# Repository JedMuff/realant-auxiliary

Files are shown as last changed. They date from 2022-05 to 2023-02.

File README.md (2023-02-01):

RealAnt Auxiliary
=================
robot_transparent
The RealAnt Auxiliary contains additioning documentation, improved designs and some simple walk gait code for the RealAnt designed by Ote Robotics at Aalto University (https://github.com/OteRobotics/realant).

The repository provides improvements relating to robustness and usability. These are related to the screw fittings and the repairability of the design. Design improvements included:
1. soft attachments to dampen damage to the robot (see 'stl_softparts' folder)
2. proper board mounting for easy construction (see 'stl_standard' folder)
3. access hatches for ease of use and repairability (see 'stl_standard' folder)
4. a stand for a motion tracking marker(used inreinforcement learning) (see 'stl_standard' folder)

Additionally with an improved robot design, some code was developed that utilized DYNAMIXEL AX-12A actuators to produce walking gaits and gestures the quadruped robot could use for initial functionality testing (see 'code' folder). 

Watch the youtube video here: https://www.youtube.com/watch?v=h07QOblhzB0.

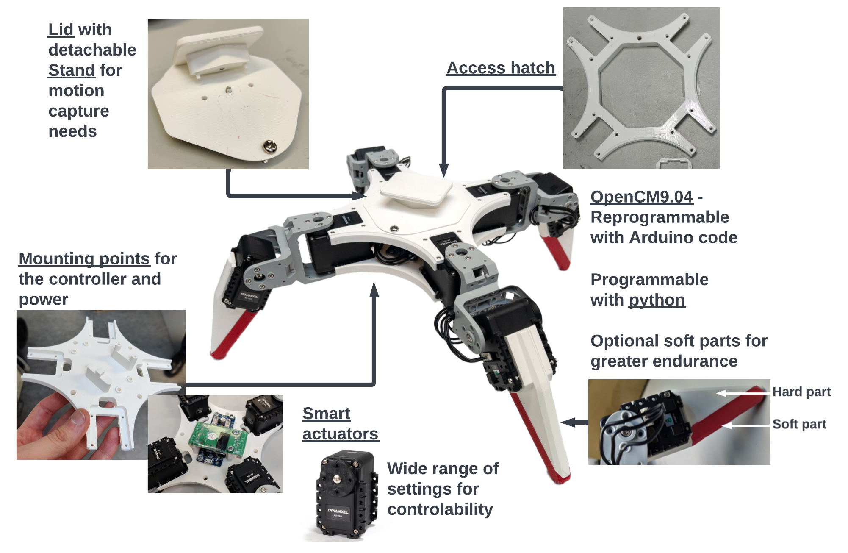
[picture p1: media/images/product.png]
product


More detailed documentation on contruction and usage where made, this can be found in the **docs** folder. 

# Structure of the GitHub
The key folders in this repository are described below, see the README kept in each directory for more details:

- **code:** Contains all the code needed for running the robot, including some simple gaits for testing.
- **docs:** Contains all the documentation for constructing and using the robot.
- **media:** Some images used in the documentation with some additional bonus images of the robot. Also contains a video made about the project. 
- **stl_softparts:** Contains the soft parts made.
- **stl_standard:** Contains the improved parts made. A modified spacer was added that improves the fit to the leg.

# Get in Contact
If you want to contribute to this repo or need any help these are the people to contact.
* Jed Muff - GitHub Managment and general help (https://www.linkedin.com/in/jed-muff/) 
* Eric Hannus - Working with the code (https://www.linkedin.com/in/eric-hannus/)
* Antti Sippola - Standard 3D printed parts (https://www.linkedin.com/in/anttisippola/)
* Julius Mikala - Soft 3D printed parts (https://www.linkedin.com/in/julius-mikala-594791178/)
# Links
**RealAnt (developed by Ote Robtics) GitHub:** https://github.com/OteRobotics/realant

**Reinforcement Learning with RealAnt** – https://github.com/AaltoVision/realant-rl

**RealAnt Auxiliary GitHub:** https://github.com/JedMuff/realant-auxiliary

**Intelligent Robotics Research Group Webpage:** https://irobotics.aalto.fi/ 

**Wiki page:** https://wiki.aalto.fi/display/AEEproject/Building+a+quadruped+robot+for+reinforcement+learning+research

**Research group page about this project:** https://irobotics.aalto.fi/building-a-quadruped-robot/

# Resources
**AX12A - EManual:** https://emanual.robotis.com/docs/en/dxl/ax/ax-12a/

**AX12 - Usermanual:** https://www.crustcrawler.com/products/bioloid/docs/AX-12.pdf

**OpenCM 9.04 - EManual:** https://emanual.robotis.com/docs/en/parts/controller/opencm904/

**Credits**:
Jed Muff, Jere Vepsä, Eric Hannus, Antti Sippola, Julius Mikala, Rituraj Kaushik, Ote Robotics

# Copyright and License

The files in this repository share files with the original [RealAnt](https://github.com/OteRobotics/realant) repository. As such the repository shares Copyright (c) 2020 with Ote Robotics Ltd and Aalto University and is licensed under MIT license. To the best of our ability we have labelled which files belong under the Ote Robotics Ltd license and which files come under the authors of this repository Copyright (c) 2023 Jed Muff, Eric Hannus, Antti Sippola, Julius Mikala, Jere Vespä.

See LICENSE for details.

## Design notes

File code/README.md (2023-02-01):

## Code Notes
The following scripts are used to test and control the robot:
-	antproxy.py
-	ant_server.py
-	tester.py
-	commander.py
-	move_set.py

The **antproxy.py** and **ant_sever.py** scripts are used to set up communication with the robot using ZeroMQ. 
These scripts are unchanged from the versions used in the original RealAnt, except for row 20 in **ant_server.py**.
which should be modified to reflect the port used for the USB connection to the robot.

The **tester.py** script is used to test individual servos, selected by their Dynamixel ID. 
The code contains functions for writing a position to a servo, testing the full motion range of a servo, and resetting 
the servos to their default positions. The script prints messages to the terminal to guide the user.

The **commander.py** requires the “keyboard” Python library. It contains functions for pre-programmed linear and rotational motion. 
The script also calls other pre-programmed actions stored in the **move_set.py** file. The W, A, S and D keys are used for linear motion,  
Q is used for counter-clockwise rotation and E for clockwise rotation, and keys 1-9 are used to run pre-programmed actions 
stored in the **move_set.py** file.

How to use:
1)	Connect power supply and USB to the robot
2)	Change line 20 in **ant_server.py** to reflect the USB port used. Default is /dev/ttyACM0.
3)	Run from the command line the following scripts: **antproxy.py**, **ant_server.py**, and **tester.py** or **commander.py**

The **ant11_cmd_dxl.ino** is the Arduino code for the OpenCM9.04 control board, and it is unchanged from the version found in the original RealAnt.

The .ino files in the folders "general_test_codes" and "servo_config_code" are not needed to run the robot, but they can be used to configure and test Dynamixel AX-12A servos via the OpenCM9.04 control board. More details are found under **/docs/dynamixel_A12A_guide.md** heading **'Accessing the Control Table via the OpenCM9.04 controller'**.

# Copyright and License

Copyright is split in this directory. Each file specifies who the copyright belongs to.

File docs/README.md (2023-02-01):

# Documentation Notes
This folder contains the following files:

- **U2d2_adapter_guide.md:** A guide on how to use the U2D2 adapter with Dynamixel Wizard 2.0 and DynamixelSDK. Used for configuring the actuators.
- **construction.md:** A step by step guide with images on how to make the robot. Also contains parts list.
- **construction.png:** An abstracted diagram showing the construction process.
- **dynamixel_A12A_guide.md:** A guide describing how the Dynamixel AX-12A servos work and how to configure them with the OpenCM board (not nessasary if using the U2d2_adapter).
- **parts_catalog.pdf:** A table showing the 3D printed parts and the setting used.
- **wiring_diagram.png:** Overall wiring diagram of the robot. The order of wiring on the boards does not matter. The ID numbers for the actuators does matter depending on the code that is used. The diagram shows what was used, with the front right actuators being 1 at the top and 2 at the bottom. This ID orientation was used to allow for easy visualization of the actuators when testing.

## Description of the Robot
The robot consists of a cover and base plates, to protect and structure the robot and legs for the robot to walk on. Both plates and leg parts are made with a 3D printer. The robot utilizes eight Dynamixel AX-12A servos for movements, two in each leg, and has eight degrees of freedom. 

Movements are sent by the Arduino based OpenCM9.04 control board and powered by a SMPS2Dynamixel power supply connector. The robot is controlled by a computer with a serial connection via USB cable using python scripts. A visual orientation tracker can be added on top of the robot's cover plate.

# Copyright and License

All documentation in realant-auxiliary/docs/ is Copyright (c) 2023 Jed Muff, Eric Hannus, Antti Sippola, Julius Mikala, Jere Vespä under MIT license. 

See LICENSE for details.See LICENSE for details.

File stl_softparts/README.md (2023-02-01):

# Some Details About Soft Parts
*For details on suggested settings to use please refer to the parts catalog (**realant-auxiliary/docs/parts_catalogue.pdf**).These settings produced suitably soft parts, as with a higher infill density was too rigid for dampening.* 

*3D printers used were either the Ultimaker S3 or S5.*

*For details about how to attach the soft parts please refer to steps 1.1 and 6.1 of the construction documentation (**realant-auxiliary/docs/construction.md**).*

The regular legs of the Real-Ant robot are reasonably fit for their intended use. However one issue identified stems from the robot's primary use: reinforcement learning. This use case makes the Real-Ant likely to make more erratic motions and even slam itself to the ground. These motions might cause some durability problems for the robot such as screws coming loose.

One solution is using thread locking fluid. The thread locking fluid only solves the issue by fastening the screws, but it does not remove the shocks caused by the robot moving. Another solution was to change the design of the robot to incorporate soft parts.

## Designs
It was observed that the soft parts needed to be situated at the bottom of the leg and the bottom plate. The soft parts at the bottom plate are required because the
robot can strike the ground with its body first. 

Several designs for both the leg and the body plates were tested before these designs where settled upon. 

The leg piece simply substitutes soft filiment where necessary.
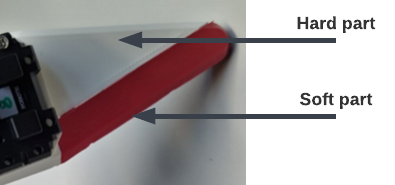
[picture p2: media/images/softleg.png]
softleg


The body plate protenction is in the form of simple soft tubes attached to the actuator connector with metal wire.
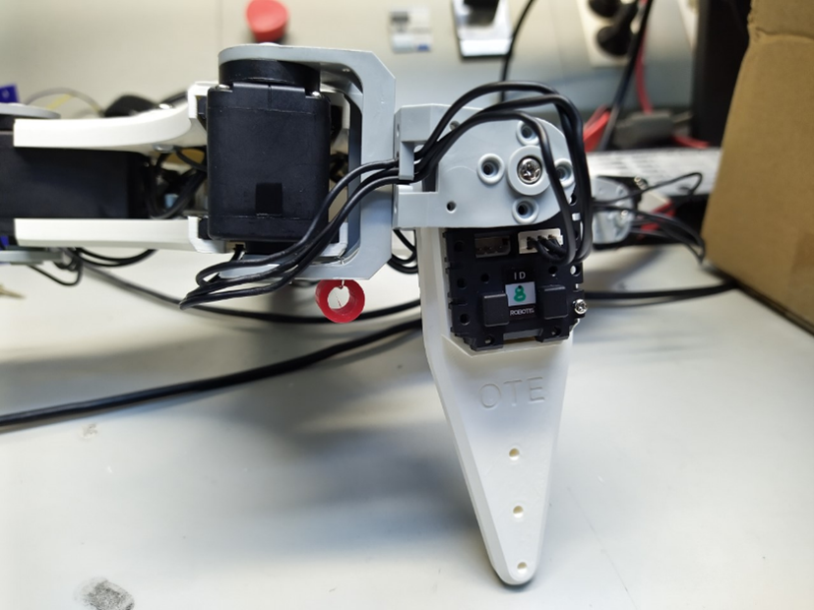
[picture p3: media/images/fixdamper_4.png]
fixdamper_4


# Copyright and License

leg.stl - Copyright (c) 2020 with Ote Robotics Ltd and Aalto University. Under MIT license. Copyright (c) 2023 Jed Muff, Eric Hannus, Antti Sippola, Julius Mikala, Jere Vespä. Under MIT license.

leg_damper.stl, round_joint_damper.stl - Copyright (c) 2023 Jed Muff, Eric Hannus, Antti Sippola, Julius Mikala, Jere Vespä. Under MIT license.

See LICENSE for details.

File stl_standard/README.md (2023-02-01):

# Details About Standard Parts

*For details about construction please refer to the construction documentation (**realant-auxiliary/docs/construction.md**).*

The body assembly of the robot serves two purposes. Firstly, it provides a structural element connecting the four leg assemblies. Secondly, it houses the electronics that power and control the actuators.

The general idea of the original body structure was kept with the new design. With the new design,the plates have similar attachments for the actuators, similar curves on the outer edges, and the actuator cables run through similar holes. However, unlike the original plates, the new design uses different parts for the top and bottom plates. This was required due to the addition of an access hatch and component mounting structures. The new design also adds parts for covering the hatch and attaching optional motion tracking markers.

# Copyright and License

bottom_plate.stl, modified_spacer.stl - Copyright (c) 2020 with Ote Robotics Ltd and Aalto University. Under MIT license.

optitrack_stand.stl, top_cover.stl, top_plate.stl - Copyright (c) 2023 Jed Muff, Eric Hannus, Antti Sippola, Julius Mikala, Jere Vespä. Under MIT license.

See LICENSE for details.

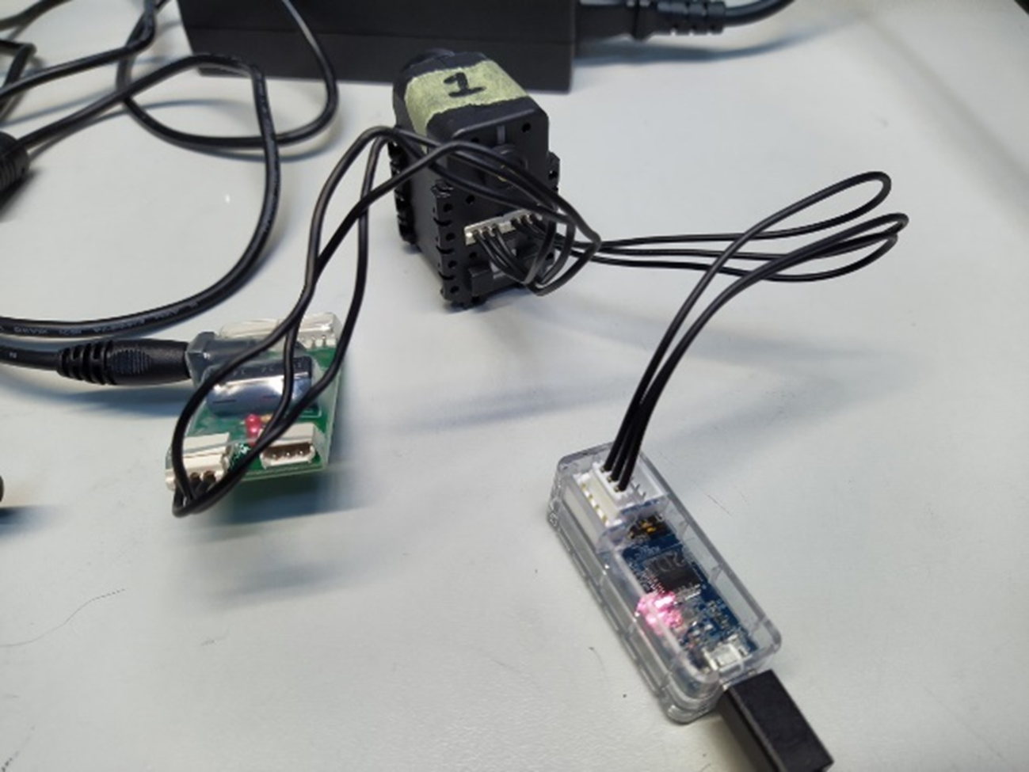
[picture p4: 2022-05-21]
media/images/U2D2_connection_2.png

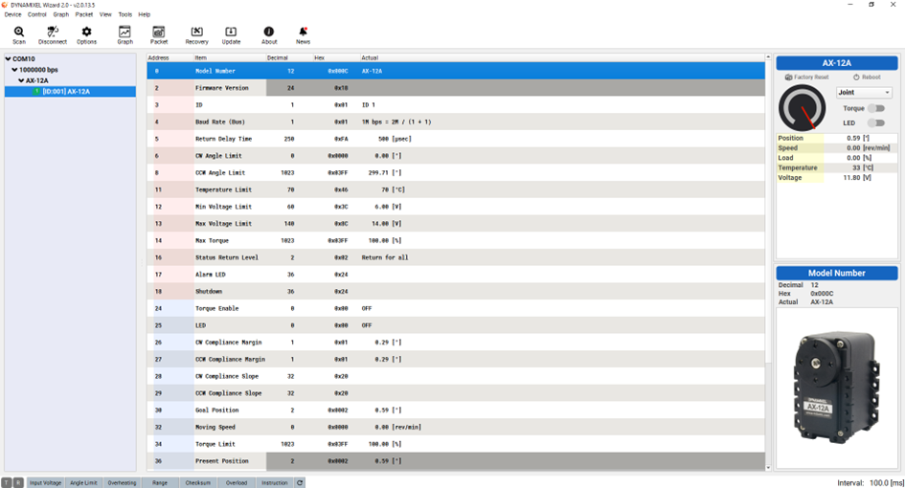
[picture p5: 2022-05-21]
media/images/Wizard_interface_1.png

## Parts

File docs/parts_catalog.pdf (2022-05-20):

## 3D Printed Parts Catalog

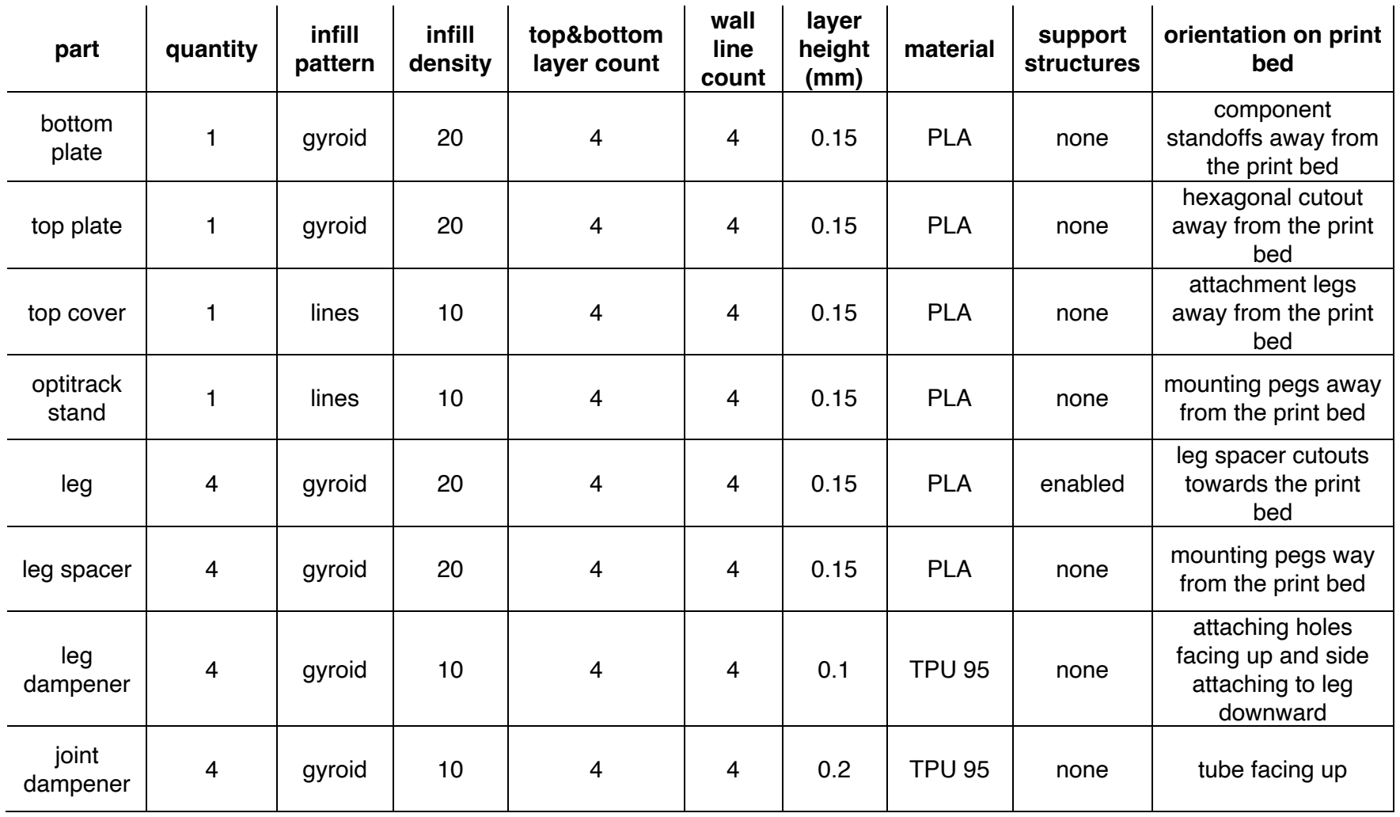
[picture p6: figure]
part; quantity; infill; pattern; infill density; top&bottom layer count; wall line count; layer height (mm); material; support; structures; orientation on print bed; bottom; plate; gyroid; PLA; none; component standoffs away from the print bed; top plate; hexagonal cutout away from the print bed; top cover; lines; attachment legs away from the print bed; optitrack; stand; mounting pegs away; from the print bed; leg; enabled; leg spacer cutouts towards the print bed; leg spacer; mounting pegs way; dampener; TPU 95; attaching holes facing up and side attaching to leg downward; joint; tube facing up

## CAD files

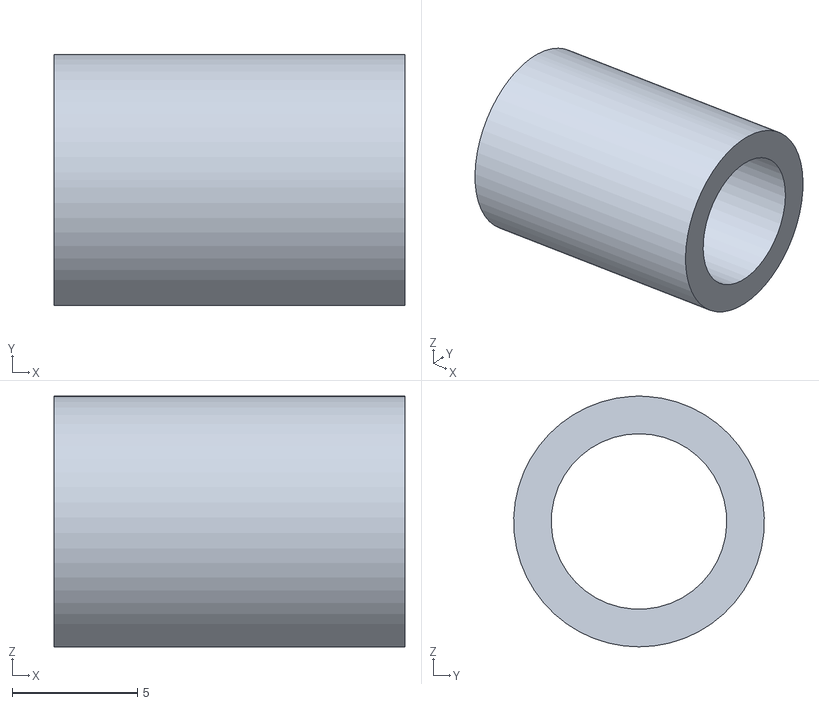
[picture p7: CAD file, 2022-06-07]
stl_softparts/round_joint_damper.stl
14.0 x 10.00 x 10.0

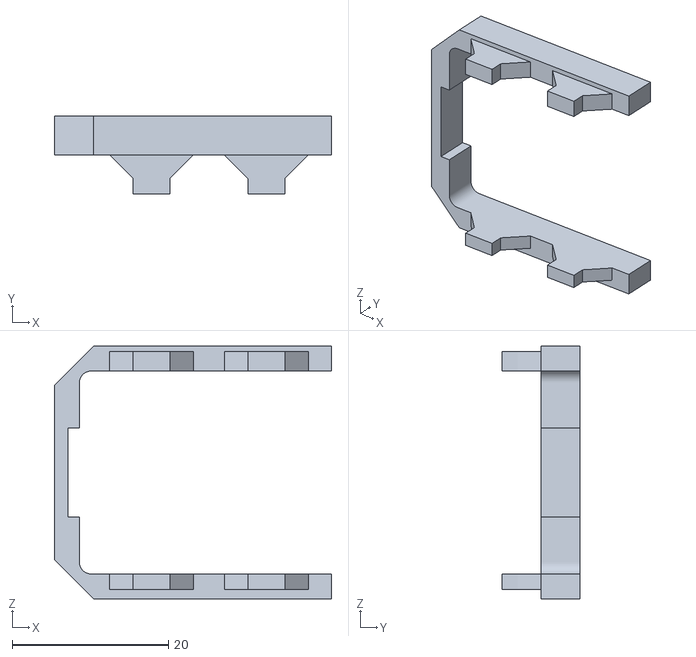
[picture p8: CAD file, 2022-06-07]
stl_standard/modified_spacer.stl
35.5 x 10.0 x 32.4

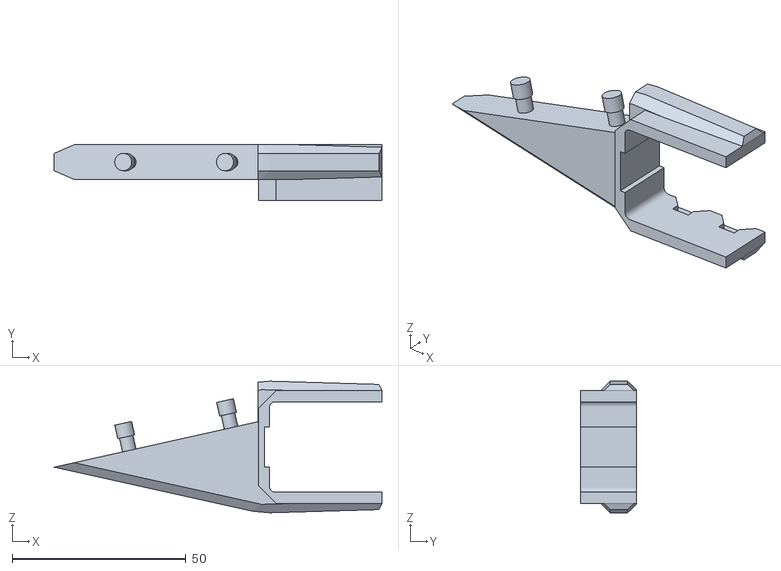
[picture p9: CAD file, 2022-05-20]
stl_softparts/leg.stl
94.3 x 16.0 x 37.9

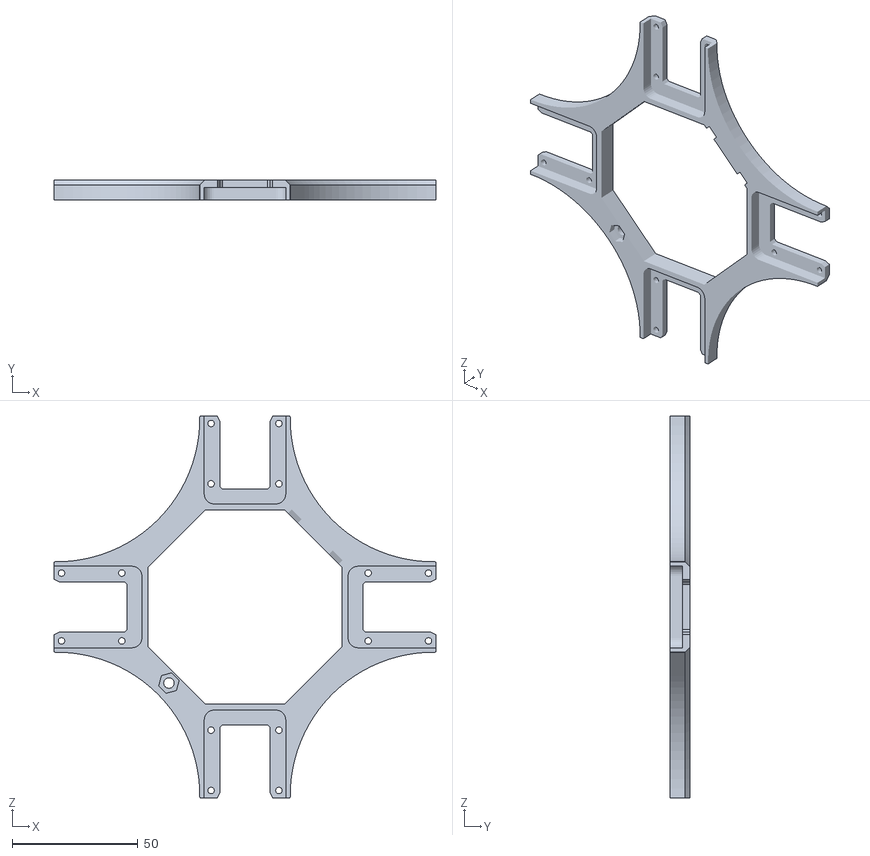
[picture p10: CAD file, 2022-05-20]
stl_standard/top_plate.stl
152.0 x 8.00 x 152.0

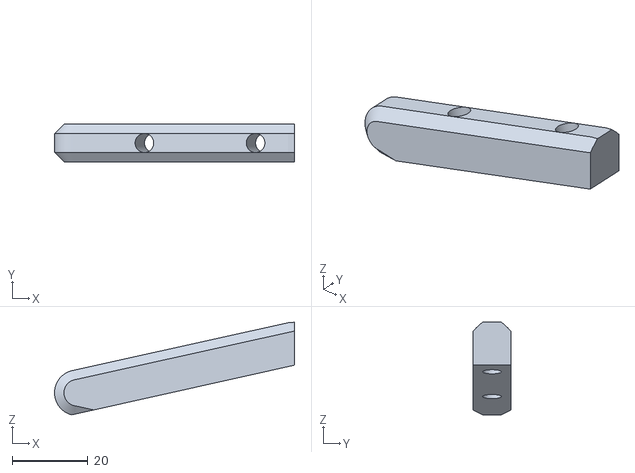
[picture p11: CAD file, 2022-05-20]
stl_softparts/leg_damper.stl
63.2 x 10.0 x 24.4

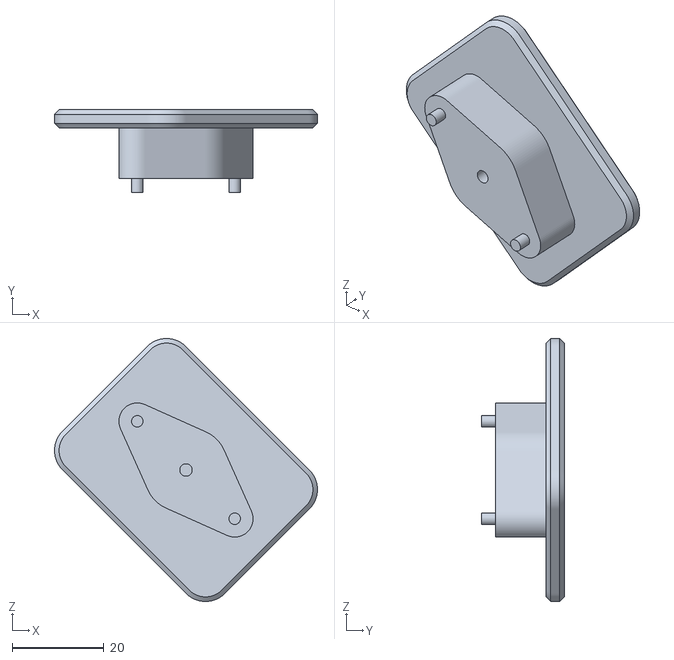
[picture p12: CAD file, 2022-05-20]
stl_standard/optitrack_stand.stl
57.3 x 18.0 x 57.3

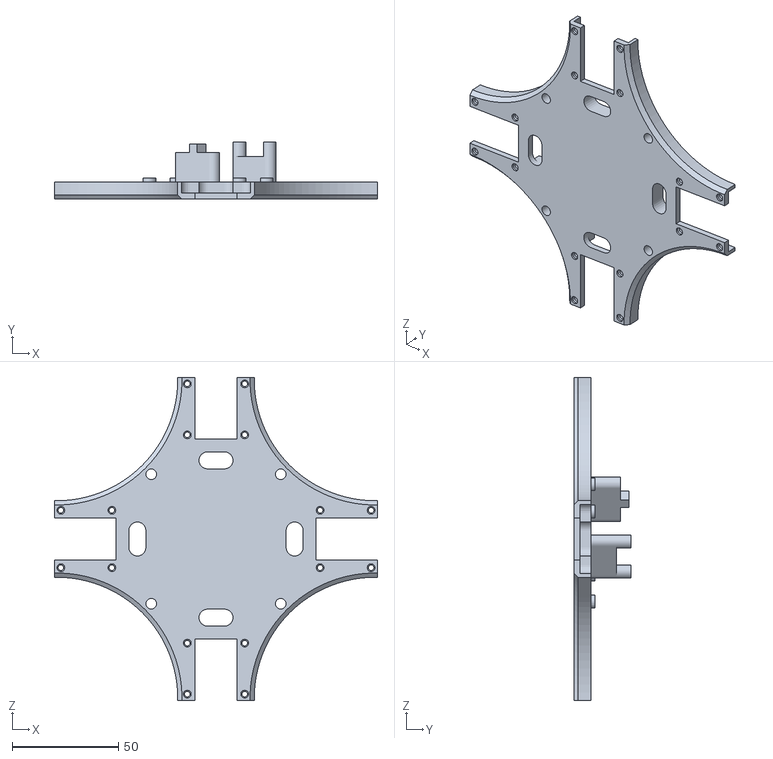
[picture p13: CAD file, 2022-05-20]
stl_standard/bottom_plate.stl
152.0 x 27.0 x 152.0

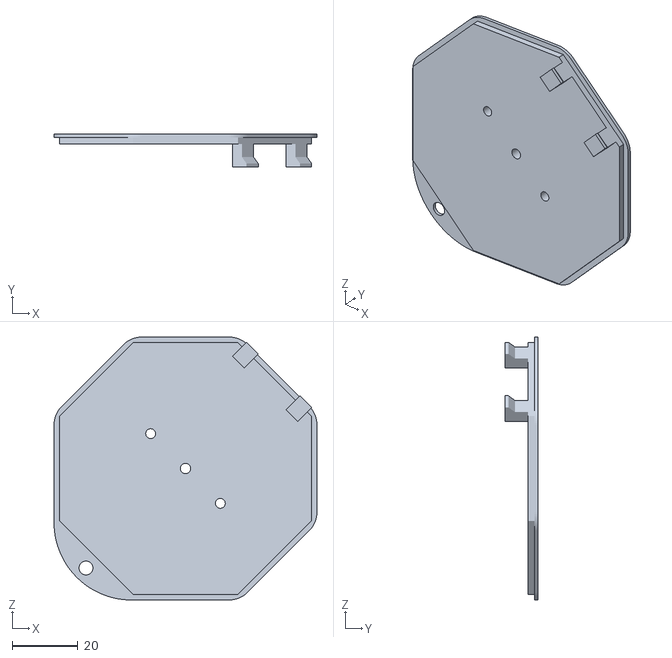
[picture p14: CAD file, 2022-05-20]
stl_standard/top_cover.stl
80.0 x 10.0 x 80.0

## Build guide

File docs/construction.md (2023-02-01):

# Preliminary Configuration of the Electronic Parts
## OpenCM9.04 Board

1.	U2D2 adapter or Arduino Uno
2.	OpenCM9.04 Board
3.	Dynamixel AX12 Actuators
4.	If U2D2 adapter, also need the appropriate wires
5.	If Arduino Uno, need Arduino USB connector and 3 Male to Female jumper wires

**Step 1 Configuring the Actuators -** The actuators need to be set up so that they have IDs ranging from 1 to 8 and no set limits. This can be done by either using the U2D2 adapter or an Arduino Uno. For each method please refer to the following documents:

* **U2D2 adapter**: “How to use the U2D2 adapter with Dynamixel Wizard 2.0 and DynamixelSDK”
* **Arduino Uno**: “Guide to Dynamixel AX-12A servos”

**Step 2 Configuring OpenCM board** - Install Arduino and setup Robotis OpenCM9.04 board support (refer to [OpenCM 9.04 e-manual](https://emanual.robotis.com/docs/en/parts/controller/opencm904/) 8.3. Arduino IDE) , and then upload the OpenCM9.04 firmware from ant11_cmd_dxl folder in this GitHub.

# Construction
## Parts Needed
1.	OpenCM9.04 Board
2.	Dynamixel AX12 Actuators (x8)
3.	Dynamixel AX12 Screws (that come with Dynamixel AX12s)
4.	Dynamixel AX12 support frames (that come with Dynamixel AX12s)
5.	Dynamixel AX/MX series (TTL) wire (x9)
6.	3D printed leg (x4) – Standard or soft version
7.	3D printed leg spacer (x4)
8.	3D printed Bottom body Plate
9.	3D printed Top Body plate
10.	SMPS2Dynamixel Board
11.	10mm M4 screws (x4)
12.	10mm M3 screws (x2)

## Optional Parts
1.	Steel wire
2.	Joint damper (x4)
3.	3D printed lid
4.	10 mm M4 screw
5.	M4 Nut
6.	3D printed stand
7.	10 mm M3 screw
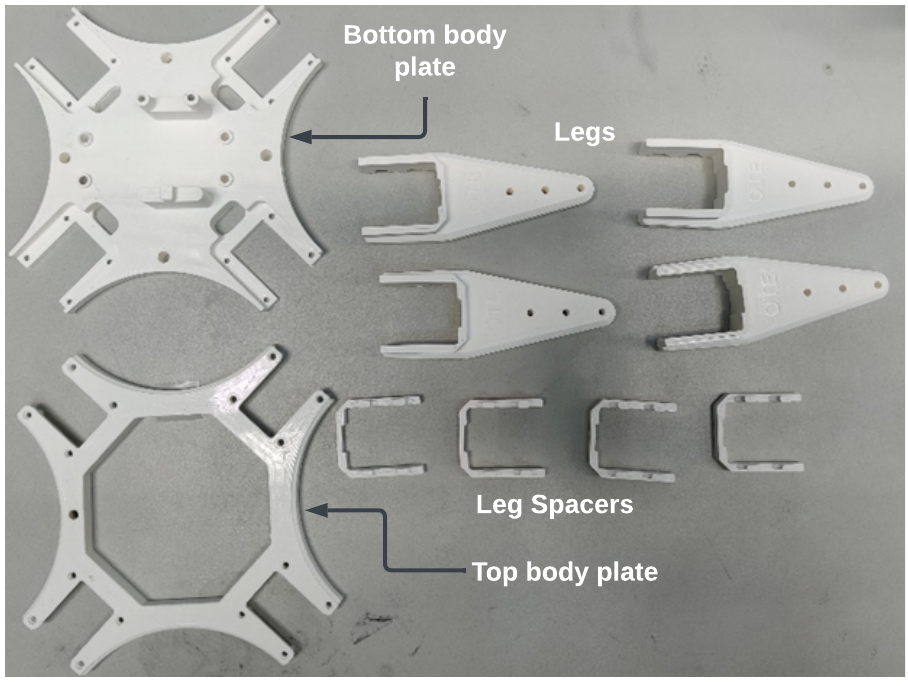
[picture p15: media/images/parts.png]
Parts


**Step 1 Priming the Legs** - The leg spacers need to be attached to the legs. To do this you may need to sand down the grooves in the leg and use a mallet to push the spacer into place. Don't apply too much force however as it may break the print. A smooth connection between the two needs to be ensured so that there is enough space to slide onto the actuator. This is done for all 4 legs.
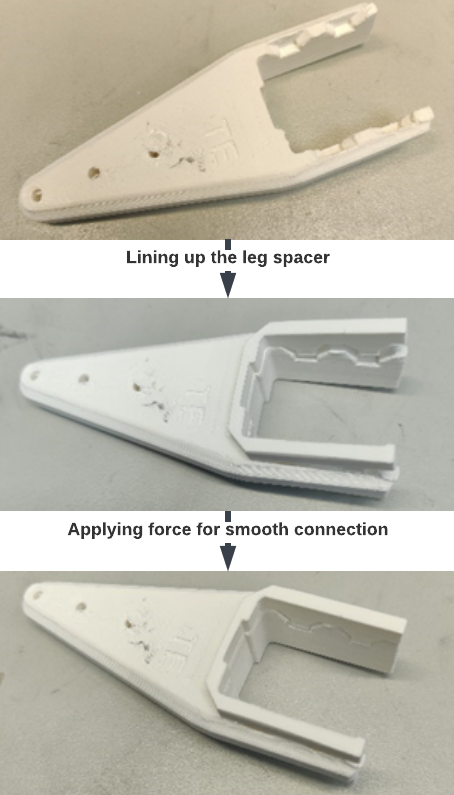
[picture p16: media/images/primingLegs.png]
primingLegs


**Step 1.1 (Optional) Fixing the soft Legs** - If you have opted for the soft legs, this is where the attachments are fitted on. This is simply done by sliding it onto the leg.

softleg

**Step 2 Priming the OpenCM Board** - Solder on the TTL headers (x4 all facing the same direction) onto the OpenCM Board.

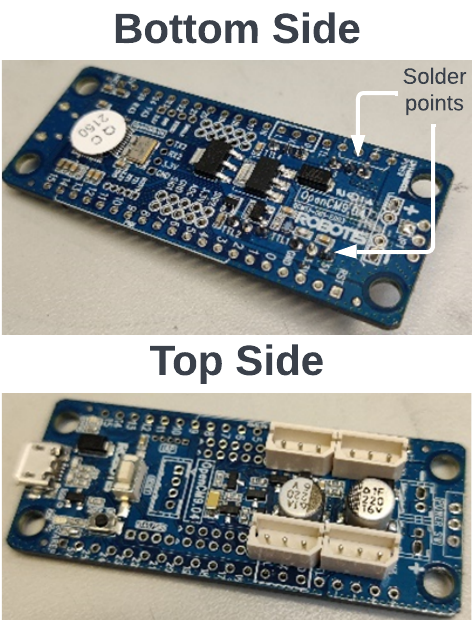
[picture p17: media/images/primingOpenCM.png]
primingOpenCM


**Step 3 Priming the SMPS2Dynamixel Board** - The SMPS2Dynamixel Board is prepared by cutting small holes in the film where 2 screw holes are. It is the two screw holes closest to the power connector. These holes are needed for mounting the board.
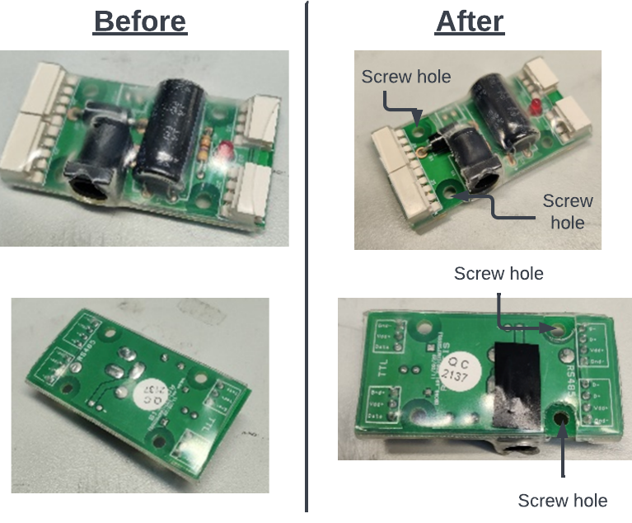
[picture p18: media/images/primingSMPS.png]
primingSMPS


**Step 4 Attaching the Legs to the Actuators** - The legs are attached to the actuators through friction. The legs should slide onto the actuators with a bit of force. If the grip seems too loose, then screws can be used to add more friction. This is done for all 4 legs.
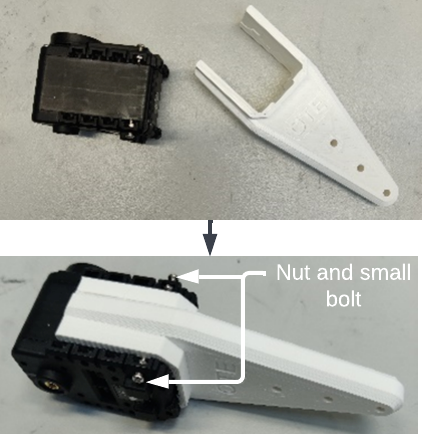
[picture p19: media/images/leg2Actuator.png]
leg2Actuator


**Step 5 Connecting the Support Frames** - Support frames are provided with the AX12's, along with screws. These first need to be connected with screws and bolts, 4 for each 2 supports for 1 leg. 16 screws and bolts are used overall for each leg.

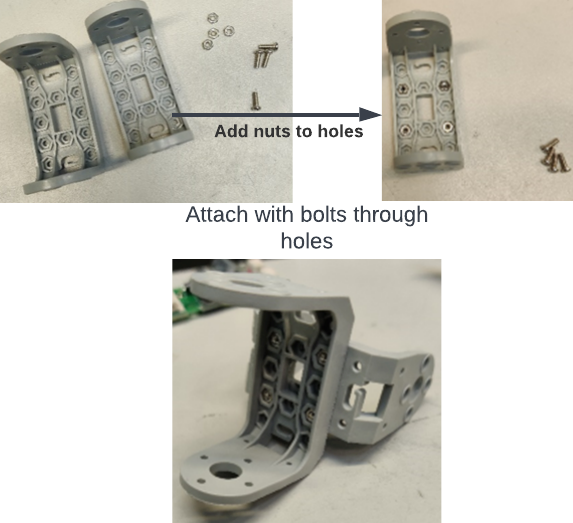
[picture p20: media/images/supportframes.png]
supportframes


**Step 6 Final Construction of the Leg** - Next the support frames are connected to the actuators, this is done once again with screws. Each connection requires 1 bigger screw and washer on one side and 4 smaller screws on the other. This is done for all 4 legs.

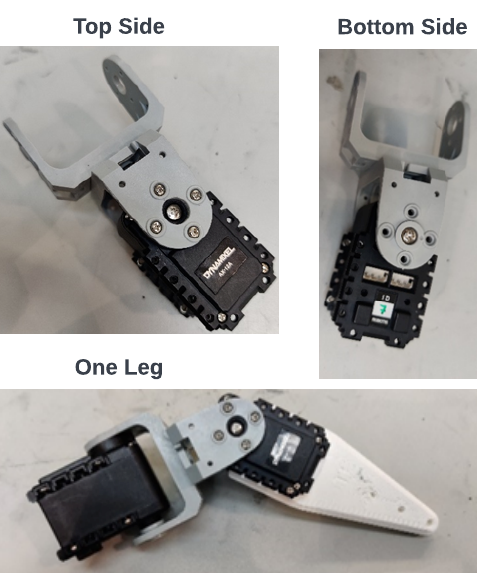
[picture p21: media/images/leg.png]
leg


**Step 6.1 (Optional) Fixing the Dampers** - 
1. Fit the joint damper to a piece of steel wire and push the wire through the holes in the plastic frame:
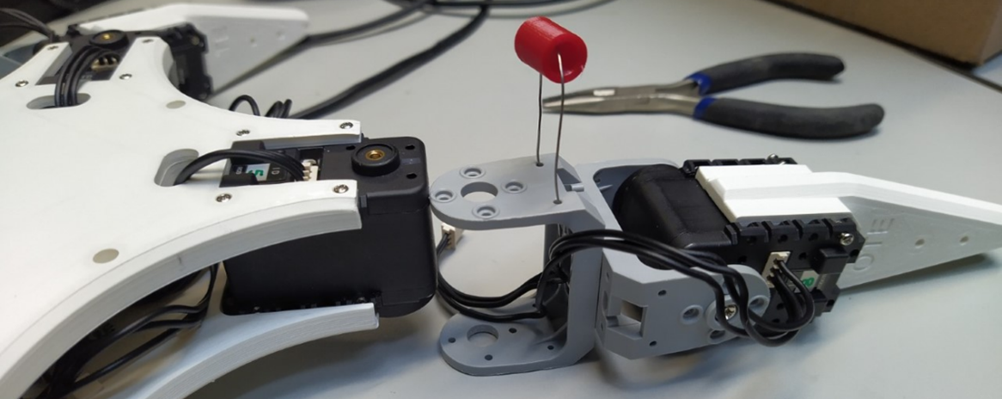
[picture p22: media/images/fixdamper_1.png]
fixdamper_1

1. Push the wire through and tighten it from the inside of the frame by twisting the steel wire:
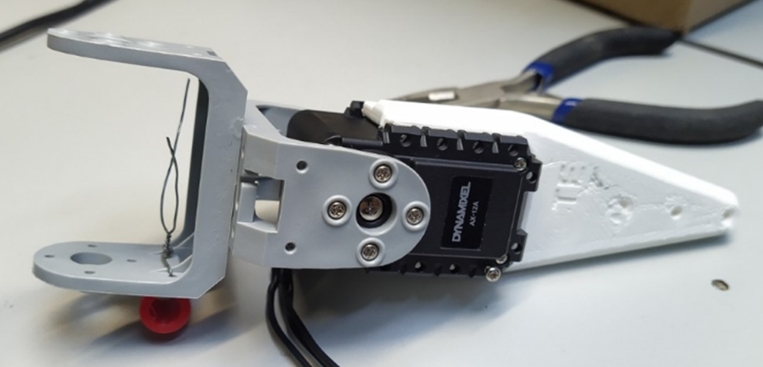
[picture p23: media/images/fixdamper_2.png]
fixdamper_2

3. Cut off any excess length of steel wire so it does not interfere with the joint movement, and finally re-attach the leg:
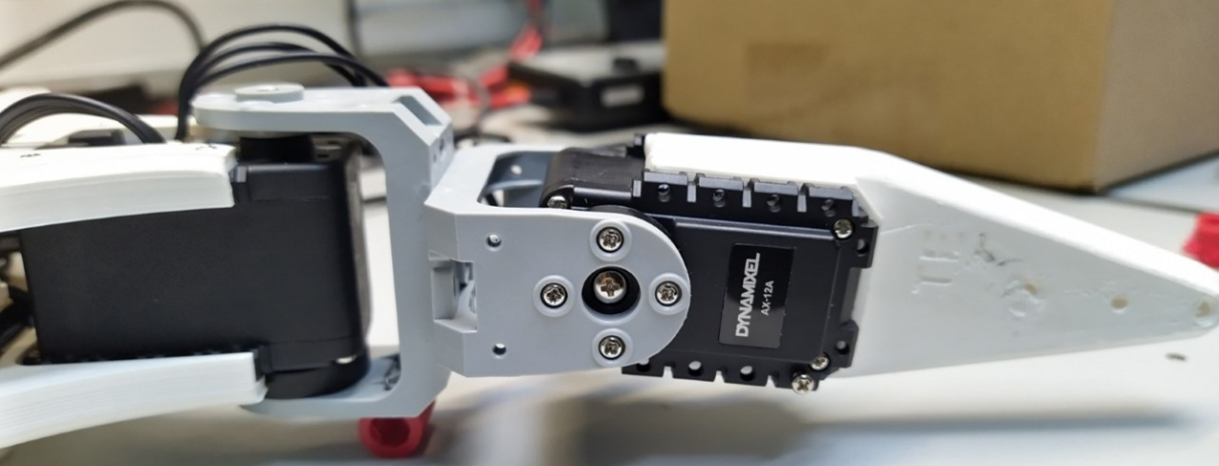
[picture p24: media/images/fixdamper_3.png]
fixdamper_3

4. Note that the wire cannot be routed through the slot in the frame piece closer to the body, as the joint damper is in the way. Route the wires through the slot in the other frame piece and try to keep the wire as tight as possible (while still allowing full motion of the joint!) near the body of the servo so that the wires do not drag under the robot:
fixdamper_4
**Step 7 Fit the Bottom Plate** - The bottom plate is fitted by simply by screwing it in the top actuators with screws provided by the AX12's.
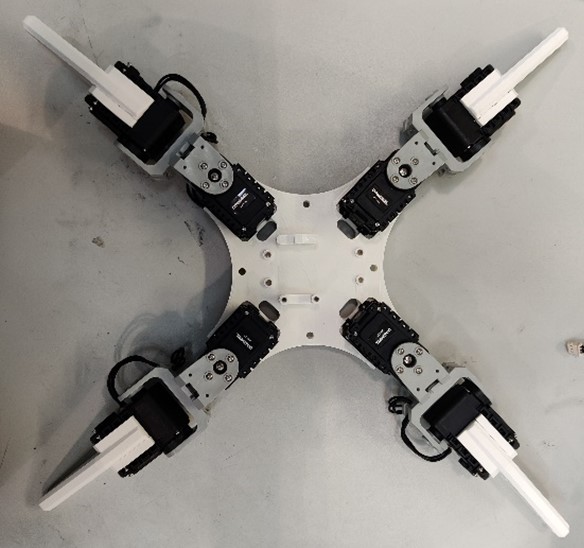
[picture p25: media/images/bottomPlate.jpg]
bottomPlate

**Step 8 Fit the OpenCM Board** - The OpenCM board is fitted with 4 10mm M4 screws. To screw the board in a bit of force is required to drill into the 3D printed holes.
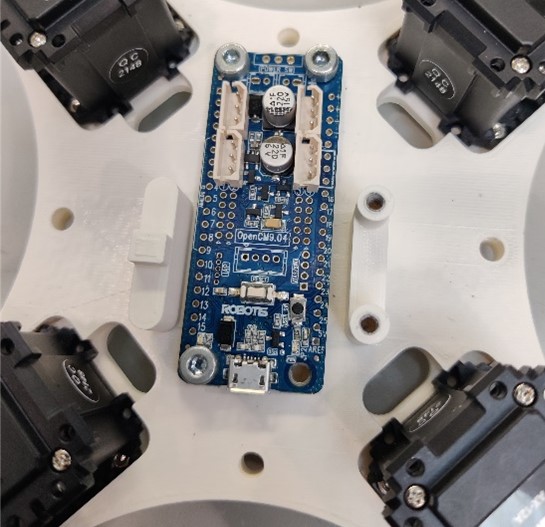
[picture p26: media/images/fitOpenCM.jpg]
fitOpenCM

**Step 9 Fit the SMPS2Dynamixel Board** - Next the SMPS2Dynamixel Board is fitted on top. Ensure it is facing the right direction and has the right orientation. Screw it in with 2 10mm M3 screws, it may require a bit of force to drill the screws into the drill holes.
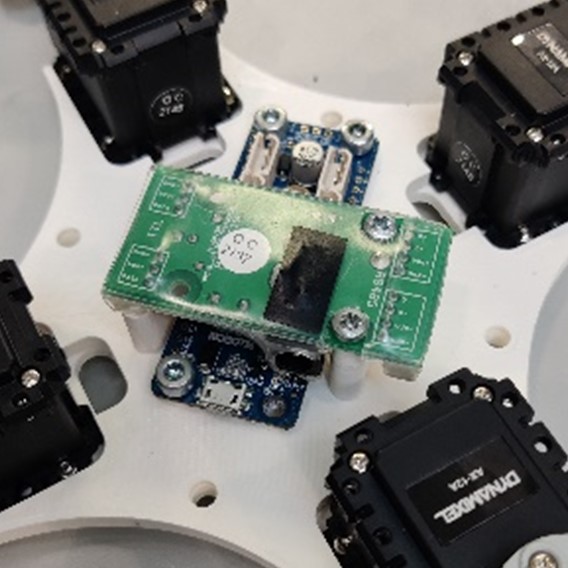
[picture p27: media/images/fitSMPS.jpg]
fitSMPS

**Step 10 Wire up the Robot** - Now the main structure is made, the wires can be connected in a neat orderly fashion. The Dynamixel AX-12A's are linked in a daisy chain fashion, it does not matter with port is used. One cable needs to be connected from the SMPS2Dynamixel board to the OpenCM Board, again it does not matter which port is used. Another cable is connected from the SMPS2Dynamixel board to an actuator (does not matter which as long as it is one at the top of the leg) and then all other top leg actuators are connected to the OpenCM board. 
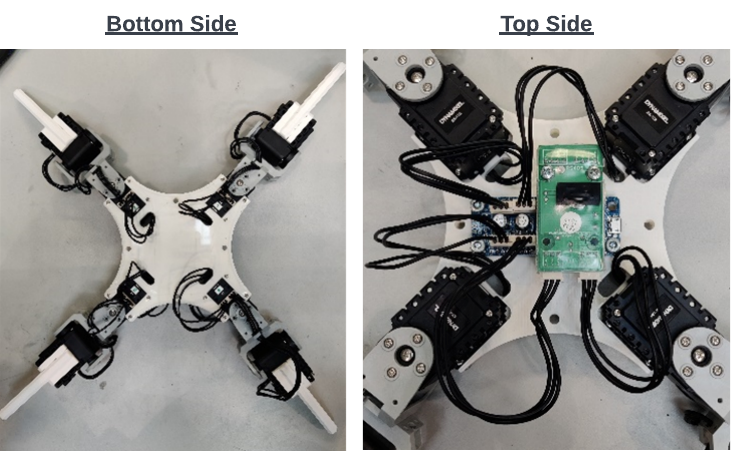
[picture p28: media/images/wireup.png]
wireup

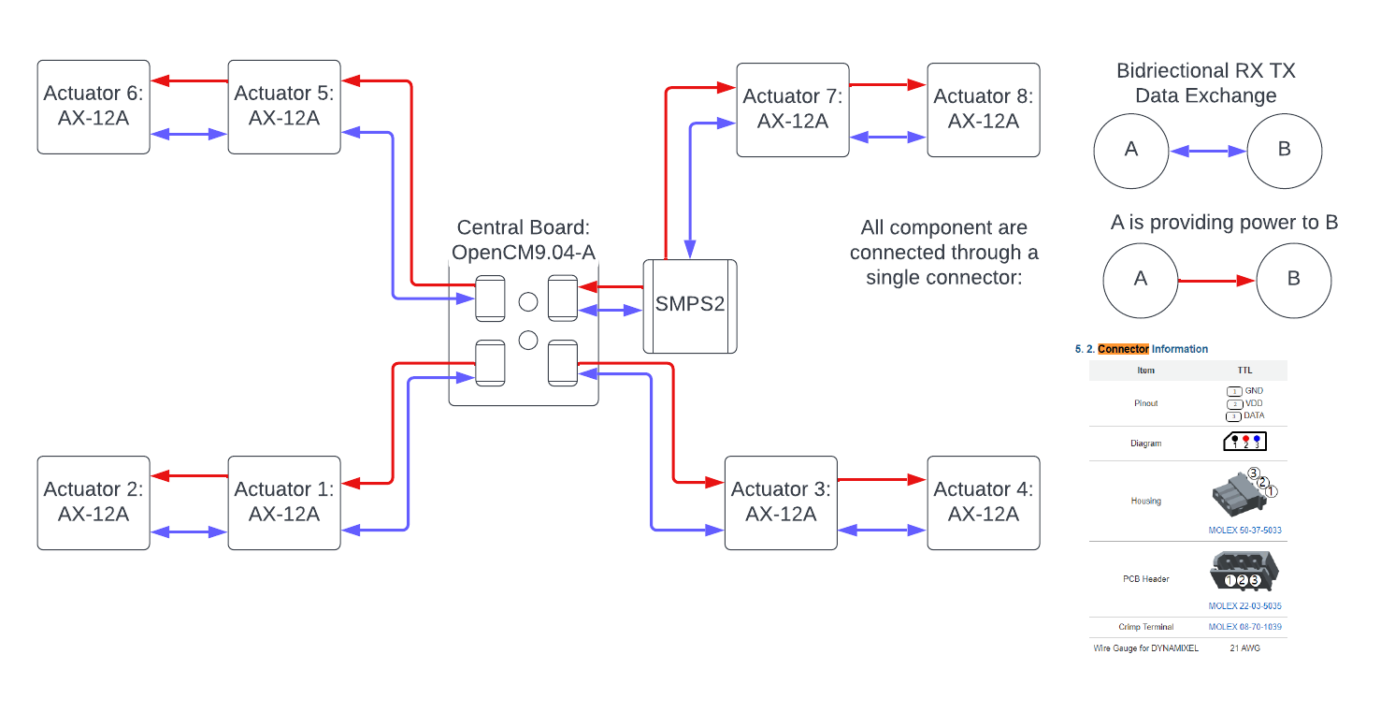
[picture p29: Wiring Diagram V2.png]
Wiring


**Step 11 Fit the Top Plate** - The top plate is fitted by simply by screwing it in the top actuators with screws provided by AX12's.
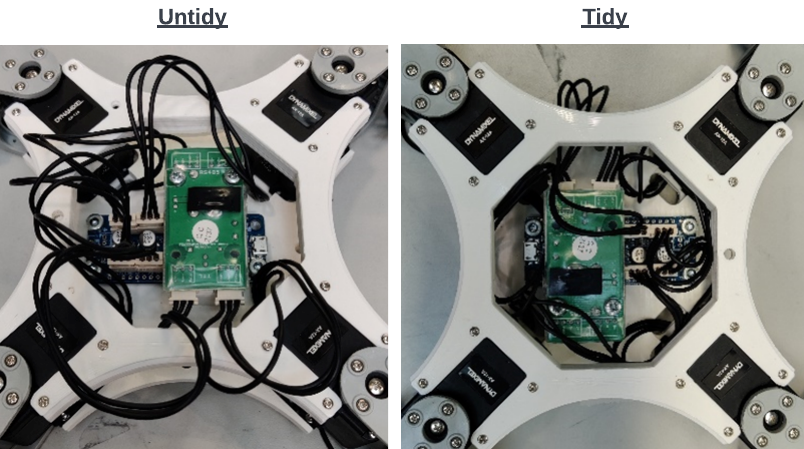
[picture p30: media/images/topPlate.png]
topPlate


**Step 12 (Optional) Adding the Lid** - The lid can be added by screwing it in with a 1 10 mm M4 screw and a M4 Nut.
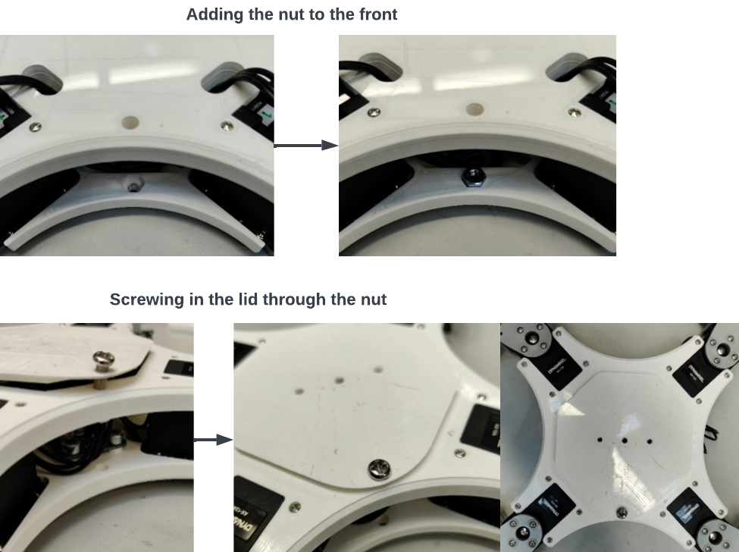
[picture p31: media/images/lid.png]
lid


**Step 13 (Optional) Adding the Stand** - The stand can be added using a 10 mm M3 screw, some force may be required to drill into the screw hole. The lid needs to be removed to perform this step.
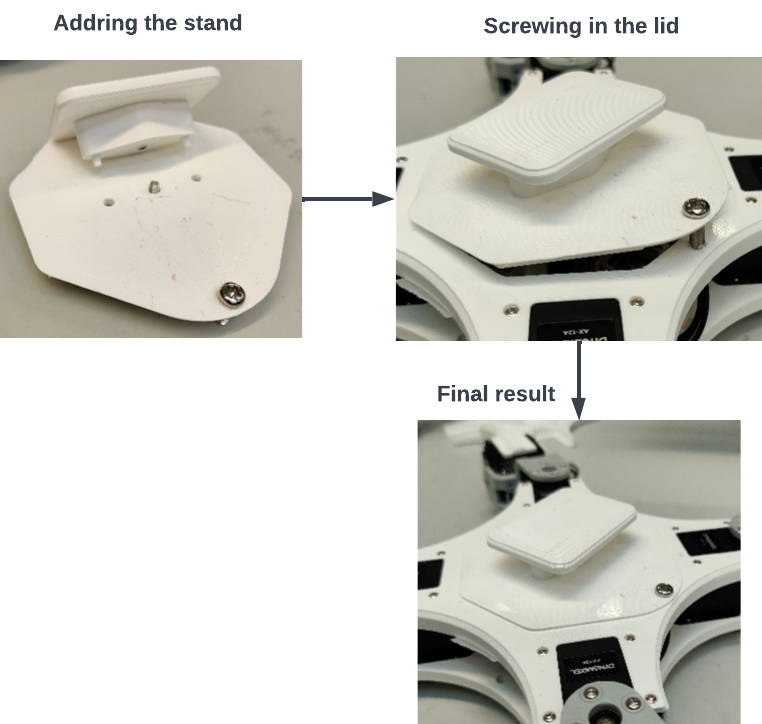
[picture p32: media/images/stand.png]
stand


# Copyright and License

Licensed under MIT licence, see LICENSE for details.
Copyright (c) 2023 Jed Muff, Eric Hannus, Antti Sippola, Julius Mikala, Jere Vespä under MIT license.

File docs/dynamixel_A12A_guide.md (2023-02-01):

# Guide to Dynamixel AX-12A servos

## The AX-12A Control Table
The AX-12A servos contain onboard memory, allowing the user to read the status of the motor or write configuration settings to it. This data is presented in the Control Table, which is divided in two fields: one for data stored in the non-volatile EEPROM and one for data stored in the volatile RAM. The control table, which is presented in the online e-Manual, also contains information about the default settings, as well as whether the address is read-write or read-only. Next some especially important control table addresses in the EEPROM are presented, which need to be considered when configuring the AX-12A servos, e.g., in the Real-Ant robot. Below is a subset of the table presented in the e-Manual:

|Address|Size (Byte)|Data Name|Description|Access|Initial value|
|---|---|---|---|---|---|
|3|1|ID	|DYNAMIXEL ID|RW|1| 
|4|1|Baud Rate|Communication Speed|RW|1| 
|6|2|CW Angle Limit|Clockwise Angle Limit|RW|0|
|8|2|CCW Angle Limit|Counter-Clockwise Angle Limit|RW|1023|

The DYNAMIXEL ID is used to identify the device in the network on the Dynamixel bus, and must thus be a unique value for each device. Thus, the default ID of 1 must be changed if multiple AX-12 servos are used. **The DYNAMIXEL ID 200 is the default ID for the OpenCM9.04 controller and should thus not be assigned to any other device.**

The Baud Rate determines the communication speed on the Dynamixel network (servos and a control board), and the initial value of 1 corresponds to 1 000 000 bps. For the baud rate of other values see the e-Manual.

The clockwise and counter-clockwise angle limits are used to limit the rotation range.  The initial values of 0 and 1023 should not limit the joint motion, but if the servos for some reason have restricted motion when they are taken in use, this parameter should be checked and changed if necessary. See picture from e-Manual below for angles corresponding to range 0 – 1023:

TheRealestAnt

## Accessing the Control Table via the OpenCM9.04 controller
The OpenCM9.04 is a microcontroller used in conjunction with the Dynamixel servos (other options are also possible via e.g. standard Arduino controllers and expansion boards). If a OpenCM9.04 “A Type” board is acquired, it will have no buses connected, so the “OpenCM9.04 - Connectors and Accessory Set” needs to be acquired and the Dynamixel bus connectors need to be soldered manually. The AX-12A servos also need **external power** (while the OpenCM9.04 itself can be powered via USB), so this needs to be arranged for the controller e.g., via the SMPS2Dynamixel adapter. See the OpenCM9.04 e-Manual for instructions for how to solder the connectors.

The OpenCM9.04 is programmed via the Arduino IDE, and functions for the Dynamixel servos are found in the Dynamixel2Arduino Library.  The OpenCM9.04 e-Manual contains detailed instructions how to configure the Arduino IDE and install the library, and the library contains useful example code under File->Examples->Dynamixel2Arduino in the IDE, but below some functions of the library needed to configure the Dynamixels are highlighted.

The example codes start off with code that needs to be altered depending on the hardware used. Pay attention to the comments; if the OpenCM904 board is used without any expansion boards the examples will have to be edited so that serial is Serial1 (not Serial3 as by default) and DXL_DIR_PIN is 28 (not 22 as by default). The correct ID also needs to be selected, if it has been changed to some other ID from the default value of 1. Finally, the correct Dynamixel protocol version must be selected (for the Real-Ant project protocol version 1.0 was used).
 
TheRealestAnt

When the communication is started by calling dxl.begin(), this function takes the baudrate as its input. In the examples the baudrate is 57600 bps, but if the Dynamixels are used with their default settings the baudrate will be 1 000 000 bps, so it needs to be changed when calling the function as pictured below:

TheRealestAnt 

The dxl.setID() can be used to set a new ID (New_ID in the picture below) for the Dynamixel servo, provided the current ID (DXL_ID in the picture below) is known. AX-12A servos should have ID = 1 when coming from the factory, but if previously used servos are used, look at the label in case the previous user has written down a new ID.

TheRealestAnt

Using the dxl.setOperatingMode() function we set the mode to “OP_POSITION”, i.e. position mode, which also reset the CW and CCW Angle limits to 0 and 1023 respectively. 

TheRealestAnt 

The current value of any Control Table address can be read and printed to the Ardunio Serial monitor (remember to use correct baudrate in the monitor!) this way:

TheRealestAnt 

Other address parameter names than ID, CW_ANGLE_LIMIT and CCW_ANGLE_LIMIT presented above can be found in the OpenCM9.04 e-Manual under 8.4.1.1 Dynamixel2Arduino Class > ReadControlTableItem(), or in the following link: https://emanual.robotis.com/docs/en/popup/arduino_api/readControlTableItem/. 

If writing directly to the control table is needed, e.g. to set some CW and CCW limits if full range of motion is not desired, a similar function called writeControlTableItem() can be used. This function can also be found in the OpenCM9.04 e-Manual under 8.4.1.1 Dynamixel2ArduinoClass > WriteControlTableItem(), or in the following link:
https://emanual.robotis.com/docs/en/popup/arduino_api/writeControlTableItem/ 

See **/code/servo_config_code/** and **/code/general_test_codes/** for examples.
## Sources:
AX-12A e-Manual: https://emanual.robotis.com/docs/en/dxl/ax/ax-12a/  
OpenCM9.04 e-Manual: https://emanual.robotis.com/docs/en/parts/controller/opencm904/  
OpenCM9.04 Accessory Set: https://www.robotis.us/opencm9-04-connectors-and-accessory-set/  
SMPS2Dynamixel adapter: https://www.robotis.us/smps2dynamixel/  

# Copyright and License

Licensed under MIT licence, see LICENSE for details.
Copyright (c) 2023 Jed Muff, Eric Hannus, Antti Sippola, Julius Mikala, Jere Vespä under MIT license.

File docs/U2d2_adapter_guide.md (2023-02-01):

# How to use the U2D2 adapter with Dynamixel Wizard 2.0 and DynamixelSDK

## Connections:
1)	Connect the U2D2 to the computer via the provided USB-MicroUSB cable.
2)	Connect the U2D2 to the Dynaxmixel AX-12A servo using the 3-pin TTL cable.
3)	Power the servo(s) with a switched-mode power supply (SMPS), via the SMPS2Dynamixel board, using another 3-pin cable.

  
         
## Configuring the servo in Dynamixel Wizard 2.0
Install the DynamixelWizard 2.0 program following the instructions for your operating system in https://emanual.robotis.com/docs/en/software/dynamixel/dynamixel_wizard2/.  
In the wizard click options and select for which settings you want to scan for servos:  

 
For example, the range of baud rates or IDs can be reduced for faster if you know what you are looking for. Scan for Dynamixels. When the servo(s) you have connected are found you will see a list of Dynamixels to the left and the settings of the chosen servo in the middle of the screen:  


To change a parameter, select the parameter from the list, select a value from the list opening in the bottom right corner, and press “Save”. The following picture shows changing the ID to 2. Other parameter settings can be changed in a similar way.  
  
In the **top right corner**, you can turn the indicator led on the servo on and off, and you can **rotate the servo to a chosen position by clicking on the black/grey/red dial.**

## Using the DynamixelSDK library 
Using the U2D2 you can directly run Python code for the Dynamixel servos. Example code can be found in the DynamixelSDK GitHub https://github.com/ROBOTIS-GIT/DynamixelSDK. For example, the **DynamixelSDK > python > tests > protocol1_0 > read_write.py** example can be used to get the servo rotating between the minimum and maximum position set in the code. However, first the correct parameters for the AX-12A model servo must be set by modifying the code: 

ADDR_MX_TORQUE_ENABLE = 24  
ADDR_MX_GOAL_POSITION = 30  
ADDR_MX_PRESENT_POSITION   = 36  
DXL_ID	= 1 #or something else if it has been changed  
BAUDRATE = 1000000 #or e.g. 57600 if it has been changed  
DXL_MAXIMUM_POSITION_VALUE  = 1023 #changed from 4000, as 1023 is the maximum for AX-12A  
DEVICENAME = 'COM10' #or something else depending on the port and OS used in the computer  

To use the DynamixelSDK examples you must install the library, for example by running **“pip install dynamixel_sdk” on Windows.** 

## For more information see:
U2D2 e-Manual: https://emanual.robotis.com/docs/en/parts/interface/u2d2/  
SMPS2Dynamixel: https://www.robotis.us/smps2dynamixel/  
Dynamixel Wizard 2.0 e-Manual: https://emanual.robotis.com/docs/en/software/dynamixel/dynamixel_wizard2/  
DynamixelSDK: https://github.com/ROBOTIS-GIT/DynamixelSDK  

# Copyright and License

Licensed under MIT licence, see LICENSE for details.
Copyright (c) 2023 Jed Muff, Eric Hannus, Antti Sippola, Julius Mikala, Jere Vespä under MIT license.

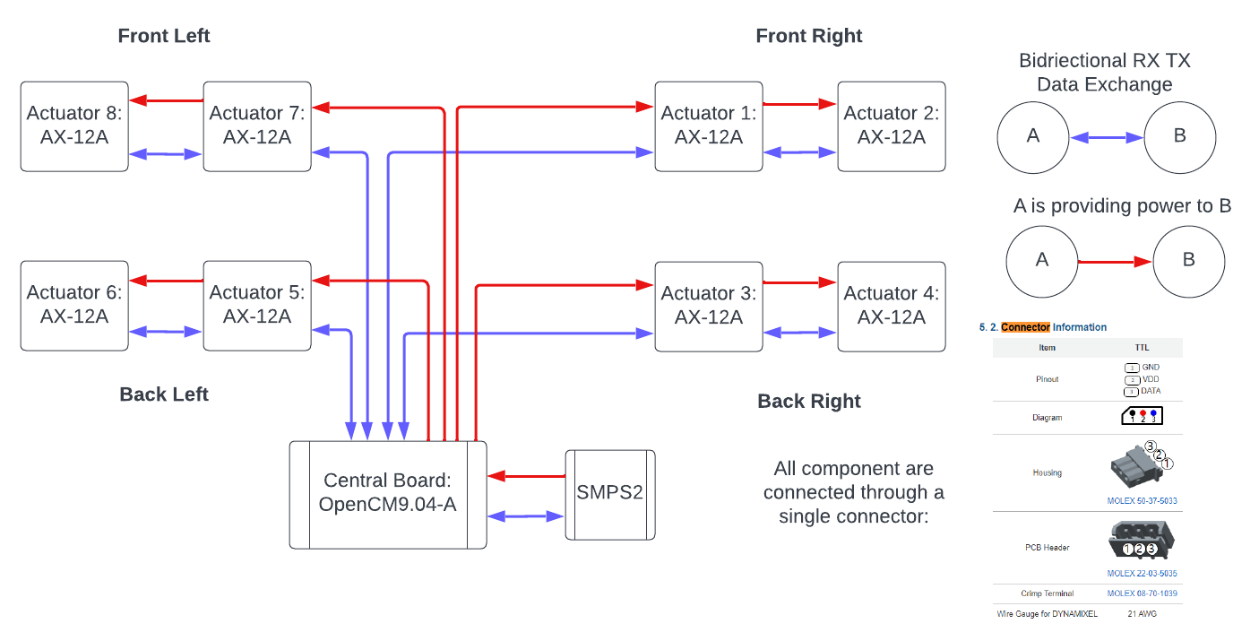
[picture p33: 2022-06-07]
docs/wiring_diagram.png

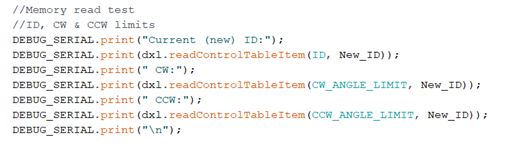
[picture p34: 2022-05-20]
media/images/AX-12A_guide_code_5.png

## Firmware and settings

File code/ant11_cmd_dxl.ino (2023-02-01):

// Licensed under MIT licence, see LICENSE for details.
// Copyright Ote Robotics Ltd. 2020

// log: 
//  20180114 - the ant has risen! all the servos turning at once consume about 4A @ 5V (!)
//  20180819 - hw functions properly
//  20180821 - cmd interface
//  20181218 - added feet contact pins
//  20190329 - added serial1 for bt connectivity
//  20200423 - build fixes for arduino 1.8.12 teensyduino 1.51
//  20201025 - dynamixel & opencm conversion
// OpenCM9.04 version

//#include <DynamixelWorkbench.h>
#include <DynamixelSDK.h>

// AX-series Control table address
#define ADDR_AX_TORQUE_ENABLE           24                 // Control table address is different in Dynamixel model
#define ADDR_AX_GOAL_POSITION           30
#define ADDR_AX_TORQUE_LIMIT            34
#define ADDR_AX_PRESENT_POSITION        36
#define ADDR_AX_PRESENT_TEMPERATURE     43

// Protocol version
#define PROTOCOL_VERSION                1.0                 // See which protocol version is used in the Dynamixel




#if defined(__OPENCM904__)
  #define DEVICE_NAME "1" //Dynamixel on Serial3(USART3)  <-OpenCM 485EXP
#elif defined(__OPENCR__)
  #define DEVICE_NAME ""
#endif

#define BAUDRATE  1000000



int servopos[] = {512, 512, 512, 512, 512, 512, 512, 512};


// feet contact pins 33-36 (plywood), (white ant pins 29-32)

//const int feet_contact_pins[] = {29,30,31,32};

String inputString = "";         // a String to hold incoming data
bool stringComplete = false;  // whether the string is complete

dynamixel::PortHandler *portHandler = NULL;
dynamixel::PacketHandler *packetHandler = NULL;

void read_servo_positions()
{
  int dxl_comm_result = COMM_TX_FAIL;
  uint8_t dxl_error = 0;  
  const char *log;

  uint8_t pos_failures = 0;
  uint8_t temp_failures = 0;

  bool result = false;

    //unsigned long start_read = millis();

    Serial.print("meas ");

    Serial.print(millis());
    Serial.print("\t");

  
    for (int i = 1; i <= 8; i++) {
      uint16_t get_data = servopos[i-1]; // backup estimate

      dxl_comm_result = packetHandler->read2ByteTxRx(portHandler, i, ADDR_AX_PRESENT_POSITION, (uint16_t*)&get_data, &dxl_error);
      if (dxl_comm_result != COMM_SUCCESS)
      {
        pos_failures |= 1<<(i-1);
      }

      Serial.print(get_data);
      Serial.print("\t");
    }


    for (int i = 0; i < 8; i++) {
      Serial.print(servopos[i]);
      Serial.print("\t");
    }

    for (int i = 0; i < 4; i++) {
      Serial.print(0); //not digitalRead(feet_contact_pins[i]));
      Serial.print("\t");
    }

    // temps
    for (int i = 1; i <= 8; i++) {
      int8_t get_data = 0;

      // uncomment for checking out servo temperatures
      //dxl_comm_result = packetHandler->read1ByteTxRx(portHandler, i, ADDR_AX_PRESENT_TEMPERATURE, (uint8_t*)&get_data, &dxl_error);
      //if (dxl_comm_result != COMM_SUCCESS)
      //{
        //Serial.println("- Failed to get present temperature");
      //  pos_failures |= 1<<(i-1);
      //}

      Serial.print(get_data);
      Serial.print("\t");
    }
    
    Serial.println();

    //Serial.print("- read took ");
    //Serial.println((millis() - start_read));


    if (pos_failures > 0)
    {
        Serial.print("- Failed to get present position 0x");
        Serial.println(pos_failures, HEX);  
    }
    if (temp_failures > 0)
    {
        Serial.print("- Failed to get present temperature 0x");
        Serial.println(temp_failures, HEX);  
    }    
}

unsigned long last_time_millis = 0;

void setup() {
    int dxl_comm_result = COMM_TX_FAIL;
    uint8_t dxl_error = 0;
    const char *log;
    bool result = false;

    portHandler = dynamixel::PortHandler::getPortHandler(DEVICE_NAME);
    packetHandler = dynamixel::PacketHandler::getPacketHandler(PROTOCOL_VERSION);


    inputString.reserve(200);

    Serial.begin(115200);
    while(!Serial);
    Serial.println("RealAnt says hello - ant11_cmd_dxl 2020-10-25");

    // Open port
    if (portHandler->openPort())
    {
      Serial.print("- Succeeded to open the port!\n");
    }
    else
    {
      Serial.print("- Failed to open the port!\n");
    }
  
    // Set port baudrate
    if (portHandler->setBaudRate(BAUDRATE))
    {
      Serial.print("- Succeeded to change the baudrate!\n");
    }
    else
    {
      Serial.print("- Failed to change the baudrate!\n");
    }

    for (int i = 1; i <= 8; i++) {

        dxl_comm_result = packetHandler->write2ByteTxRx(portHandler, i, ADDR_AX_TORQUE_LIMIT, 512, &dxl_error);
        if (dxl_comm_result != COMM_SUCCESS)
        {
          packetHandler->getTxRxResult(dxl_comm_result);
          Serial.println("- Failed set torque limit (1)");
          
        }
        else if (dxl_error != 0)
        {
          packetHandler->getRxPacketError(dxl_error);
          Serial.println("- Failed set torque limit (2)");
        }
        else
        {
          Serial.println("- Succeeded to set torque limit");
        }
    }
      
}

String getValue(String data, char separator, int index)
{
    int found = 0;
    int strIndex[] = { 0, -1 };
    int maxIndex = data.length() - 1;

    for (int i = 0; i <= maxIndex && found <= index; i++) {
        if (data.charAt(i) == separator || i == maxIndex) {
            found++;
            strIndex[0] = strIndex[1] + 1;
            strIndex[1] = (i == maxIndex) ? i+1 : i;
        }
    }
    return found > index ? data.substring(strIndex[0], strIndex[1]) : "";
}



void loop() {

  int dxl_comm_result = COMM_TX_FAIL;
  uint8_t dxl_error = 0;
  
  const char *log;
  bool result = false;

  while (Serial.available()) {
    char inChar = (char)Serial.read();
    inputString += inChar;
    if (inChar == '\n') {
      stringComplete = true;
    }
  }
  
  if (stringComplete) {
    Serial.print("- recv: ");
    Serial.println(inputString);

    if (inputString.startsWith("attach_servos")) {
      for (int i = 1; i <= 8; i++) {
        //result = dxl_wb.jointMode(i, 0, 0, &log);
        //if (result == false)
        //{
        //  Serial.println(log);
        //  Serial.println("- Failed to change joint mode");
        //}
        //else
        //{
        //  Serial.println("- Succeed to change joint mode");
        //} 

        
        //result = dxl_wb.torqueOn(i, NULL);
        dxl_comm_result = packetHandler->write1ByteTxRx(portHandler, i, ADDR_AX_TORQUE_ENABLE, 1, &dxl_error);

        if (dxl_comm_result != COMM_SUCCESS)
        {
          Serial.println("- Failed to change torque on");
        }
        else
        {
          Serial.println("- Succeed to change torque on");
        } 
      }
    }
    else if (inputString.startsWith("detach_servos")) {
      for (int i = 1; i <= 8; i++) {
        dxl_comm_result = packetHandler->write1ByteTxRx(portHandler, i, ADDR_AX_TORQUE_ENABLE, 0, &dxl_error);

        if (dxl_comm_result != COMM_SUCCESS)
        {
          Serial.println("- Failed to change torque off");
        }
        else
        {
          Serial.println("- Succeed to change torque off");
        } 
      }
    }
    else if (inputString.startsWith("reset")) {
      for (int i = 1; i <= 8; i++) {
        servopos[i-1] = 512;
        dxl_comm_result = packetHandler->write2ByteTxRx(portHandler, i, ADDR_AX_GOAL_POSITION, servopos[i-1], &dxl_error);
        if (dxl_comm_result != COMM_SUCCESS)
        {
          Serial.println("- Failed to set goal position (reset)");
        }
      }
    }
    else if (inputString.startsWith("standup")) {
      for (int i = 1; i <= 8; i++) {
        int val = (i % 2 == 1) ? 512 : 224;
        servopos[i-1] = val;
        dxl_comm_result = packetHandler->write2ByteTxOnly(portHandler, i, ADDR_AX_GOAL_POSITION, servopos[i-1]);
        if (dxl_comm_result != COMM_SUCCESS)
        {
          Serial.println("- Failed to set goal position (standup)");
        }
      }
      
    }
    else {
      //unsigned long start_write = millis();
  
      for (int i = 0; i < 8; i++) {
        String k = getValue(inputString, ' ', 2*i);
        String v = getValue(inputString, ' ', 2*i+1);
  
        if (k != "" && k.startsWith("s"))
        {
          int s = k.substring(1).toInt();
          if (v != "" && (s >= 1 && s <= 8))
          {
            int pos =  v.toInt();
            //Serial.print("- driving servo ");
            //Serial.print(s);
            //Serial.print(" to pos ");
            //Serial.println(pos);
            servopos[s-1] = pos;
            
            dxl_comm_result = packetHandler->write2ByteTxOnly(portHandler, s, ADDR_AX_GOAL_POSITION, servopos[s-1]);
            if (dxl_comm_result != COMM_SUCCESS)
            {
              Serial.println("- Failed to set goal position (standup)");
            }
          }
        }
      }

      //Serial.print("- write took ");
      //Serial.println((millis() - start_write));
    }



    // clear the string:
    inputString = "";
    stringComplete = false;
  }

  if ((millis() - last_time_millis) > 20) {
    read_servo_positions();
    last_time_millis = millis();
  }
}

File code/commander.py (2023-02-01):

# Licensed under MIT licence, see LICENSE for details.
# Copyright Jed Muff, Eric Hannus, Antti Sippola, Julius Mikala, Jere Vespä. 2023

# - The keypresses do not require Ctrl+C to be pressed to exit a loop  (keyboard module needed!)
#  >> The keyboard module is needed for this! Install in Windows with "pip install keyboard"
# - A separate move_set.py file is used to store moves that are called by pressing keys 1-9

import zmq #library for communication with the robot
import time #for timing
import keyboard #for reading keypresses
from move_set import * #import additional moves from a separate file called move_set.py

stepTime = 0.2 #for delays in walking function

#Movement functions
def walk(front_LU, front_LL, front_RU, front_RL, back_LU, back_LL, back_RU, back_RL):
    # The walk() function takes the indexes of the upper (close to the body) and lower (further from the body)
    # servos for the left and right leg (left and right when looking in the desired movement direction), for both 
    #the front and back legs in relation to the direction of movement.

    #_LU = left upper joint
    #_LL = left lower joint
    #_RU = right upper joint
    #_RL = right lower joint

    #The second part of the send_multipart list must be a byte string containing servo indexes (s is included before the numerical index!)
    # and corresponding setpoint values. Spaces are sepearating servo values, and the string must end with a linebreak. To convert a
    # concentrated string to a byte string, the .encode() function is used.

    #TODO: remove old lines if new ones work correctly. They are now ordered in front left > front right > back left > back right order for all commands. Also the descriptions of each movement (also in CW and CCE rotations can be exxtended/improved).
    #sock.send_multipart([b"cmd", ("s"+str(front_RL)+" 300 s"+str(back_RL)+" 300 s"+str(back_LL)+" 300 s"+str(front_LL)+" 300\n").encode('UTF-8')])
    sock.send_multipart([b"cmd", ("s"+str(front_LL)+" 300 s"+str(front_RL)+" 300 s"+str(back_LL)+" 300 s"+str(back_RL)+" 300\n").encode('UTF-8')]) #set all lower joints to 300 = wider than default
    time.sleep(stepTime)
    
    #sock.send_multipart([b"cmd", ("s"+str(front_RL)+" 375 s"+str(back_RL)+" 300 s"+str(back_LL)+" 375 s"+str(front_LL)+" 300\n").encode('UTF-8')])
    sock.send_multipart([b"cmd", ("s"+str(front_LL)+" 300 s"+str(front_RL)+" 375 s"+str(back_LL)+" 375 s"+str(back_RL)+" 300\n").encode('UTF-8')]) #lift front right and back left legs 
    #^^ here we can send to only 2 joints?
    time.sleep(stepTime)

    #sock.send_multipart([b"cmd", ("s"+str(front_RU)+" 512 s"+str(back_RU)+" 312 s"+str(back_LU)+" 512 s"+str(front_LU)+" 712\n").encode('UTF-8')]) ### Move Left
    sock.send_multipart([b"cmd", ("s"+str(front_LU)+" 712 s"+str(front_RU)+" 512 s"+str(back_LU)+" 512 s"+str(back_RU)+" 312\n").encode('UTF-8')]) #move front left and back right legs
    time.sleep(stepTime)

    #sock.send_multipart([b"cmd", ("s"+str(front_RL)+" 300 s"+str(back_RL)+" 300 s"+str(back_LL)+" 300 s"+str(front_LL)+" 300\n").encode('UTF-8')])
    sock.send_multipart([b"cmd", ("s"+str(front_LL)+" 300 s"+str(front_RL)+" 300 s"+str(back_LL)+" 300 s"+str(back_RL)+" 300\n").encode('UTF-8')]) #reset front right and back left legs that were offset previously, now all legs wide again
    #^^here we can send to only 2 joints again?
    time.sleep(stepTime)
    
    #sock.send_multipart([b"cmd", ("s"+str(front_RL)+" 300 s"+str(back_RL)+" 375 s"+str(back_LL)+" 300 s"+str(front_LL)+" 375\n").encode('UTF-8')])
    sock.send_multipart([b"cmd", ("s"+str(front_LL)+" 375 s"+str(front_RL)+" 300 s"+str(back_LL)+" 300 s"+str(back_RL)+" 375\n").encode('UTF-8')]) #lift front left and back right legs
    time.sleep(stepTime)

    #sock.send_multipart([b"cmd", ("s"+str(front_RU)+" 312 s"+str(back_RU)+" 512 s"+ str(back_LU)+" 712 s"+str(front_LU)+" 512\n").encode('UTF-8')]) ### Move Right
    sock.send_multipart([b"cmd", ("s"+str(front_LU)+" 512 s"+str(front_RU)+" 312 s"+ str(back_LU)+" 712 s"+str(back_RU)+" 512\n").encode('UTF-8')]) #move front right and back left legs that were offset previously
    time.sleep(stepTime)


def forward():
    walk(7, 8, 1, 2, 5, 6, 3, 4)

def backward():
    walk(3, 4, 5, 6, 1, 2, 7, 8)

def left():
    walk(5, 6, 7, 8, 3, 4, 1, 2)

def right():
    walk(1, 2, 3, 4, 7, 8, 5, 6)


def rotateCCW():
    sock.send_multipart([b"cmd", b"s2 300 s4 300 s6 300 s8 300\n"]) #initially set all outer joints to a wider stance than the default angle of 205
    time.sleep(stepTime)

    sock.send_multipart([b"cmd", b"s2 375 s4 300 s6 375 s8 300\n"]) #lift the lower joints of two diagonal legs
    time.sleep(stepTime)

    sock.send_multipart([b"cmd", b"s1 512 s3 312 s5 512 s7 312\n"]) #shift two legs by rotating the upper joints
    time.sleep(stepTime)

    sock.send_multipart([b"cmd", b"s2 300 s4 300 s6 300 s8 300\n"]) #reset all lower joints
    time.sleep(stepTime)

    sock.send_multipart([b"cmd", b"s2 300 s4 375 s6 300 s8 375\n"]) #lift the lower joints of the other two legs that were not lifted in the previous step
    time.sleep(stepTime)

    sock.send_multipart([b"cmd", b"s1 312 s3 512 s5 312 s7 512\n"]) #shift two legs by rotating the upper joints
    time.sleep(stepTime)

def rotateCW():
    sock.send_multipart([b"cmd", b"s2 300 s4 300 s6 300 s8 300\n"]) #initially set all outer joints to a wider stance than the default angle of 205
    time.sleep(stepTime)
    
    sock.send_multipart([b"cmd", b"s2 375 s4 300 s6 375 s8 300\n"]) #lift the lower joints of two diagonal legs
    time.sleep(stepTime)

    sock.send_multipart([b"cmd", b"s1 512 s3 712 s5 512 s7 712\n"]) #shift two legs by rotating the upper joints
    time.sleep(stepTime)

    sock.send_multipart([b"cmd", b"s2 300 s4 300 s6 300 s8 300\n"]) #reset all lower joints
    time.sleep(stepTime)
    
    sock.send_multipart([b"cmd", b"s2 300 s4 375 s6 300 s8 375\n"]) #lift the lower joints of the other two legs that were not lifted in the previous step
    time.sleep(stepTime)

    sock.send_multipart([b"cmd", b"s1 712 s3 512 s5 712 s7 512\n"]) #shift two legs by rotating the upper joints
    time.sleep(stepTime)

def reset():
    #send in two parts to prevent overload of too many commands at once
    sock.send_multipart([b"cmd", b"s1 512 s3 512 s5 512 s7 512 \n"])
    time.sleep(0.5)
    sock.send_multipart([b"cmd", b"s2 205 s4 205 s6 205 s8 205\n"])
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

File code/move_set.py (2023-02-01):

# Licensed under MIT licence, see LICENSE for details.
# Copyright Jed Muff, Eric Hannus, Antti Sippola, Julius Mikala, Jere Vespä. 2023

import zmq
import time


#Function for calling any of the action functions manually added to the move_list
def call_move(key, sock):
        index = key-1 #keystroke 1 = index 0 in list
        move_list = [wave, sideWave, scratch, empty_move, empty_move, empty_move, empty_move, empty_move, empty_move] #Update this list of moves as new functions are added!
        if index < len(move_list):
                move_list[index](sock)


#Action functions

def empty_move(sock):
        #This function is a placeholder used in move_list if no other function is used, so that something will happen when each of the keys 1-9 are pressed.
        print("No move has been added to this key yet.")
        time.sleep(1)

def wave(sock):
        print("wave") #for debugging
        # initial position
        sock.send_multipart([b"cmd", b"s1 512 s2 256 s3 552 s4 256 s5 512 s6 256 s7 472 s8 256\n"])
        time.sleep(2)
        # wave middle
        sock.send_multipart([b"cmd", b"s1 512 s2 512 s3 552 s4 256 s5 512 s6 256 s7 472 s8 256\n"])
        time.sleep(0.7)

        # -- cycle 1 -- #
        # wave up
        sock.send_multipart([b"cmd", b"s1 512 s2 612 s3 552 s4 256 s5 512 s6 256 s7 472 s8 256\n"])
        time.sleep(0.5)
        # wave down
        sock.send_multipart([b"cmd", b"s1 512 s2 412 s3 552 s4 256 s5 512 s6 256 s7 472 s8 256\n"])
        time.sleep(0.5)

        # -- cycle 2 -- #
        # wave up
        sock.send_multipart([b"cmd", b"s1 512 s2 612 s3 552 s4 256 s5 512 s6 256 s7 472 s8 256\n"])
        time.sleep(0.5)
        # wave down
        sock.send_multipart([b"cmd", b"s1 512 s2 412 s3 552 s4 256 s5 512 s6 256 s7 472 s8 256\n"])
        time.sleep(0.5)
        # -- end cycle -- #
        
        # wave middle
        sock.send_multipart([b"cmd", b"s1 512 s2 512 s3 552 s4 256 s5 512 s6 256 s7 472 s8 256\n"])
        time.sleep(0.7)
        # reset initial position
        sock.send_multipart([b"cmd", b"s1 512 s2 256 s3 552 s4 256 s5 512 s6 256 s7 472 s8 256\n"])

def sideWave(sock):
        print("sidewave") #for debugging
        # initial position
        sock.send_multipart([b"cmd", b"s1 512 s2 256 s3 552 s4 256 s5 512 s6 256 s7 472 s8 256\n"])
        time.sleep(2)
        # wave high
        sock.send_multipart([b"cmd", b"s1 512 s2 612 s3 552 s4 256 s5 512 s6 256 s7 472 s8 256\n"])
        time.sleep(0.7)

        # -- cycle 1 -- #
        # wave high left
        sock.send_multipart([b"cmd", b"s1 412 s2 612 s3 552 s4 256 s5 512 s6 256 s7 472 s8 256\n"])
        time.sleep(0.5)
        # wave high right
        sock.send_multipart([b"cmd", b"s1 612 s2 612 s3 552 s4 256 s5 512 s6 256 s7 472 s8 256\n"])
        time.sleep(0.5)

        # -- cycle 2 -- #
        # wave high left
        sock.send_multipart([b"cmd", b"s1 412 s2 612 s3 552 s4 256 s5 512 s6 256 s7 472 s8 256\n"])
        time.sleep(0.5)
        # wave high right
        sock.send_multipart([b"cmd", b"s1 612 s2 612 s3 552 s4 256 s5 512 s6 256 s7 472 s8 256\n"])
        time.sleep(0.5)
        # -- end cycle -- #
        
        # wave high
        sock.send_multipart([b"cmd", b"s1 512 s2 612 s3 552 s4 256 s5 512 s6 256 s7 472 s8 256\n"])
        time.sleep(0.7)
        # reset initial position
        sock.send_multipart([b"cmd", b"s1 512 s2 256 s3 552 s4 256 s5 512 s6 256 s7 472 s8 256\n"])

def scratch(sock):
        print("scratch") #for debugging
        # initial position
        sock.send_multipart([b"cmd", b"s1 512 s2 256 s3 512 s4 256 s5 512 s6 256 s7 512 s8 256\n"])
        time.sleep(2)

        # -- cycle 1 -- #
        # Scratch low
        sock.send_multipart([b"cmd", b"s1 512 s2 412 s3 512 s4 412 s5 512 s6 412 s7 512 s8 412\n"])
        time.sleep(0.5)
        
        # Scratch high
        sock.send_multipart([b"cmd", b"s1 512 s2 205 s3 512 s4 205 s5 512 s6 205 s7 512 s8 205\n"])
        time.sleep(0.5)
        
        # -- cycle 2 -- #
        # Scratch low
        sock.send_multipart([b"cmd", b"s1 512 s2 412 s3 512 s4 412 s5 512 s6 412 s7 512 s8 412\n"])
        time.sleep(0.5)
        
        # Scratch high
        sock.send_multipart([b"cmd", b"s1 512 s2 205 s3 512 s4 205 s5 512 s6 205 s7 512 s8 205\n"])
        time.sleep(0.7)
        # -- end cycle -- #

        # reset initial position
        sock.send_multipart([b"cmd", b"s1 512 s2 256 s3 512 s4 256 s5 512 s6 256 s7 512 s8 256\n"])

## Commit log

2022-05-20 New structure
    [body_v6.stl, leg_spacer_v8.stl, leg_v8.stl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]
2022-05-20 added files for body assembly
    [bottom_plate.stl, optitrack_stand.stl, top_cover.stl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]
2022-05-20 Create Guide to Dynamixel AX-12A servos.md
2022-05-20 Update Guide to Dynamixel AX-12A servos.md
2022-05-23 adding wiring diagram
2022-06-07 adding documents
    [Gantt chart.xlsx, round_joint_damper.stl]
2022-06-07 Update README.txt
    Added two sentences to the end for Arduino codes
2022-06-07 Added slimmer leg spacer that fits better
    [modified_spacer.stl]
2022-06-08 removing archive
    [body_v6.stl, leg_spacer_v8.stl, leg_v8.stl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]
2022-06-18 Removing appendix and including some documentation from it. Embedding the video in the main README and removing references to appendix
    [Gantt chart.xlsx]
